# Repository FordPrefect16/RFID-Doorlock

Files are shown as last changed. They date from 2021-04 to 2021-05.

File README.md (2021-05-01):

# RFID-Doorlock
A 3D-printable Doorlock which can attached to a standard door lock cylinder. Opens via RFID-Tag

Aim of this project is to create a electronic doorlock for access control and logging on an sd card. It shall be used on the door of the makerspace at our University. 

The first version of this lock will rely on a wireconnection between outer and inner parts of the lock, hopefully later versions will communicate over radio. 
STL an CAD files can be found under main.

### Short description of planed functions

The mechanism at the inside of the door is shoved over the key and can be secured with two screws at the fittings and two additional screws. Also the cylinder is secured with a press fitting. When a RFID Tag is registered at the door terminal, the tag will be compared to the entitled codes on a csv-file on sd. When access is granted, the buttons (which indicate the lockstate via LED - open or closed) can be pressed. The green one opens the lock, the red one closes it. Tag, time, date and action will be logged on a csv-file. The lockstate is retrieved through a 10 turn potentiometer, to secure right Information, even if lockstate is changed to mechanical action. The lock can be manualy overridden from inside by turning the wheel or from outside with the right key for the cylinder. 
 


# Materials used

Printed in black PLA on a Ender 3

### List of materials (inside mechanics):



- 1x cylinder with key used in door
- 1x bearing 6808 2RS / 61808 2RS 40x52x7 mm
- 1x timing belt GT2 288 mm 
- 1x timing belt GT2 174 mm
- 1x Nema 17 stepper motor 42x20 mm, 16 Ncm, 1 A, biopolar
- 1x 10K Potentiometer 10 Turn
- 5x M3*20
- 4x M3*16
- 2x M2*20 + Nut
- 6x M4*10
- 4x M3*20 countersunk head

### List of materials (controller/electronics):



- Arduino UNO <br>
- 1x power supply 9-12 V (for this setup 9 V are recomended so the A4988 driver can supply the stepper with 1 A without overheating)
- 1x jack connector for breadboard
- 1x Protobreadboard halfsized
- Dupont-connectors
- 1x 100 uF electrolyte capacitor
- 1x stepper driver (e. g. A4988) (don't forget to adjust current output for Stepper)
- 1x Adafruit MicroSD Card Breakout Board (with SPI) + micro SD (for Access control + data logging)
- 1x RTC Breakout Board - Real Time Clock

For wireless version:
- radio component(NRF24L01)

### List of materials (door terminal):



- 4x M3*4
- 4x M4*6
- 1x pieco beeper (active) 5 V
- JST-connectors
- 1x 100 uF electrolyte capacitor
- 1x button / led red, 5 V, 10 mm
- 1x button / led green, 5 V, 10 mm
- 1x PN532 NFC RFID Module Elchouse (in this setup I2C is used, don! forget to setup the switches on this breakout board)
- 1x Protobreadboard halfsized
  
For wireless version: 
- Arduino Nano
- radio component(NRF24L01)
   
### Mechanism without hull



### Circuit




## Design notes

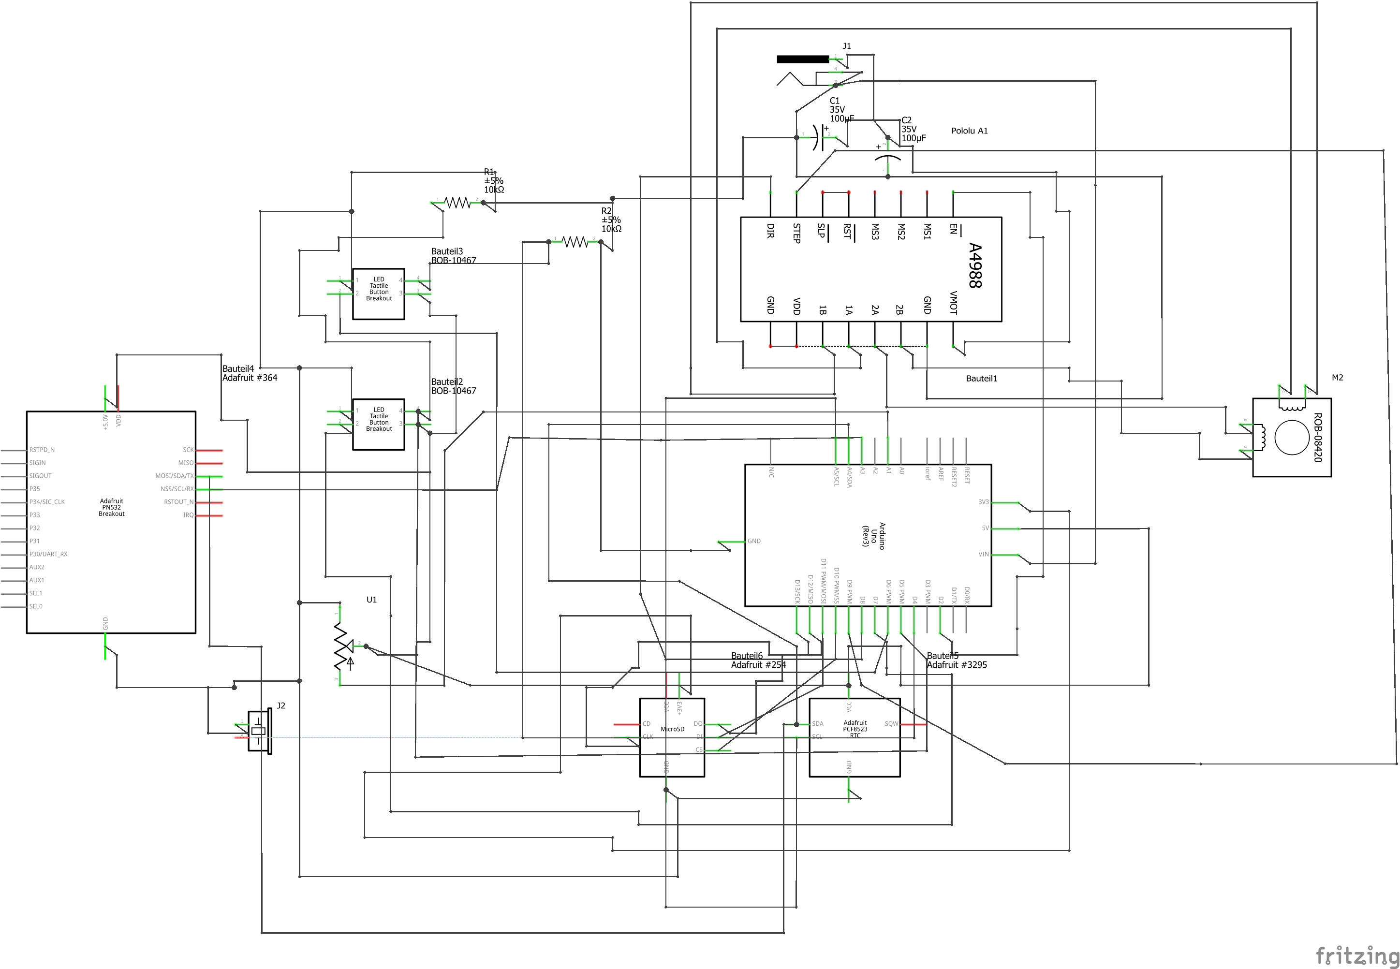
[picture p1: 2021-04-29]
Schematics/Circuit_fritzing_cable_Schaltplan.png

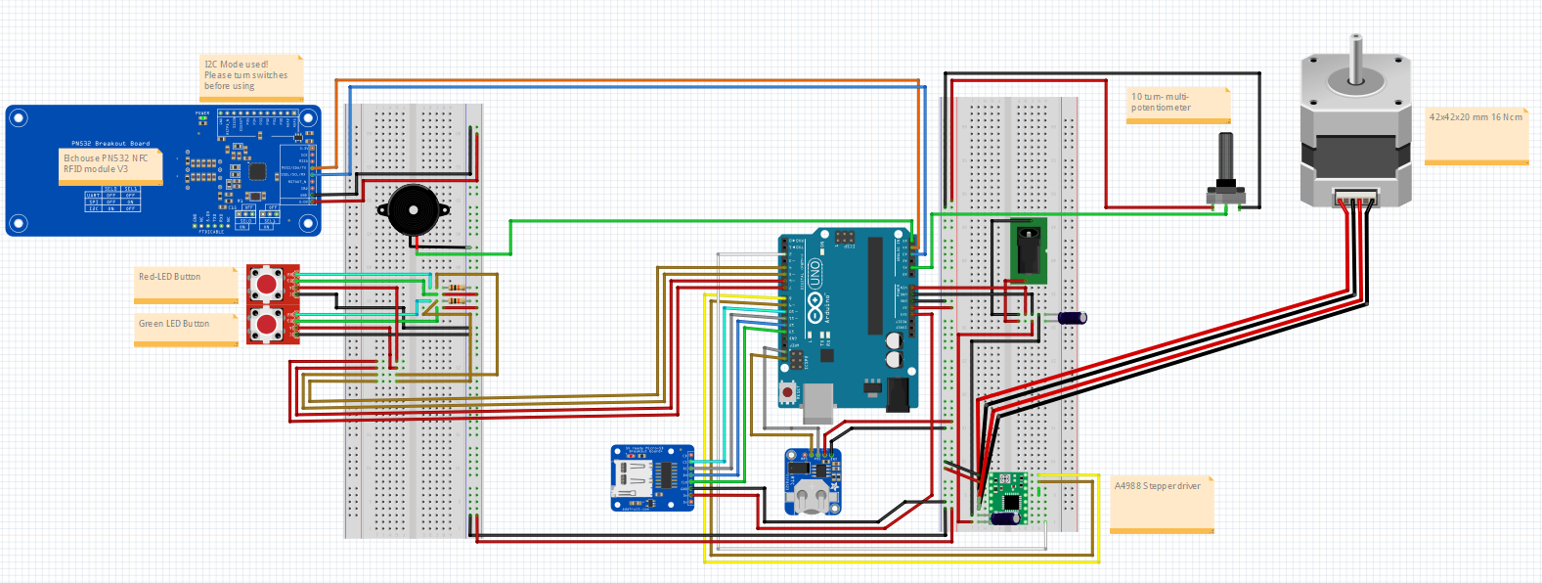
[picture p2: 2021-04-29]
Schematics/Schematics.PNG

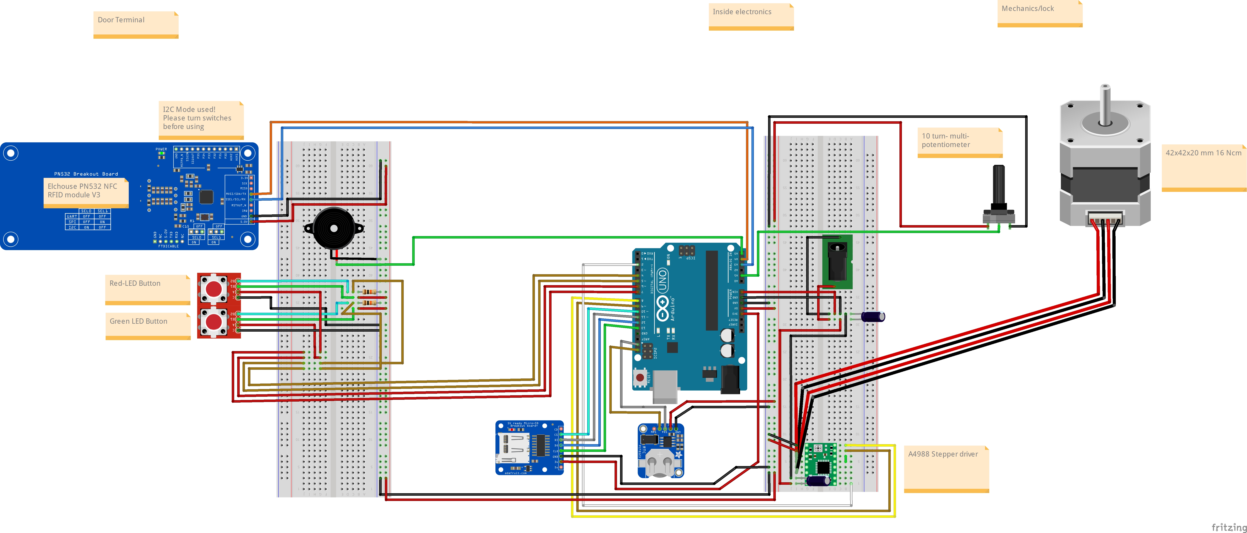
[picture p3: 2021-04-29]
Schematics/Circuit_fritzing_cable_Steckplatine.jpg

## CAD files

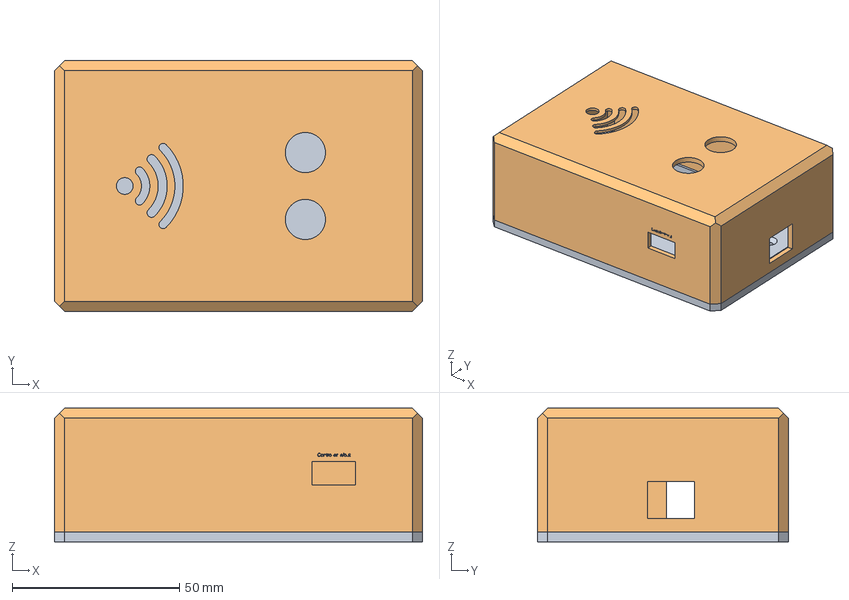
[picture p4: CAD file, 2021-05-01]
Printable Parts/CAD/DoorTerminal.step
110.0 x 75.0 x 40.0 mm

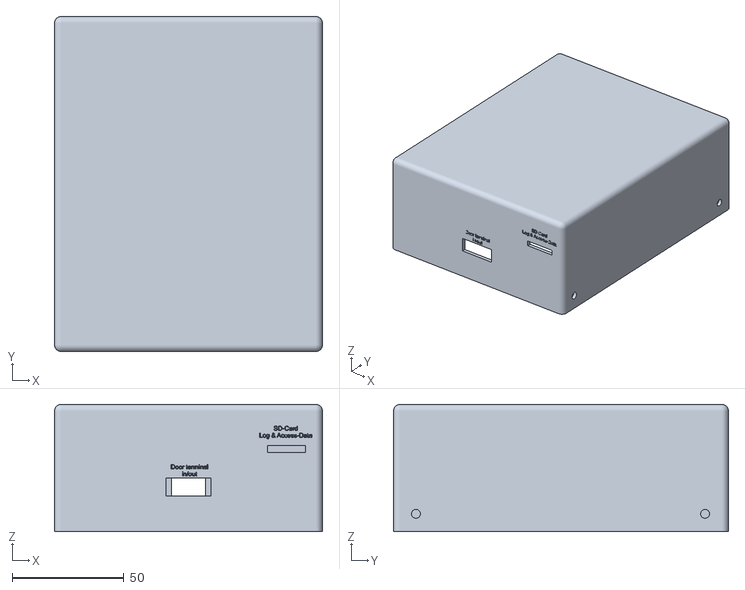
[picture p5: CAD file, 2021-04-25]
Printable Parts/ControlerElectronics/Electronics-Top.stl
120.0 x 150.0 x 57.0

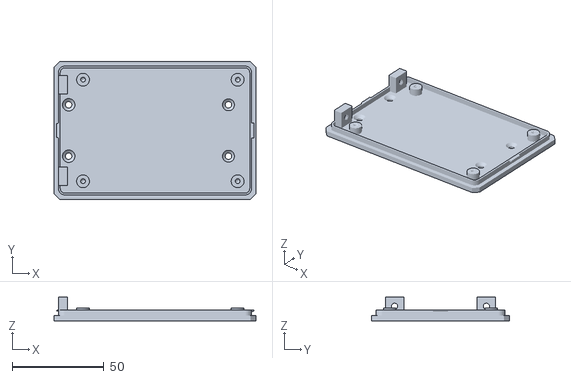
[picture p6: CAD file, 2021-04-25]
Printable Parts/Door Terminal/Door terminale base.stl
110.0 x 75.0 x 13.0

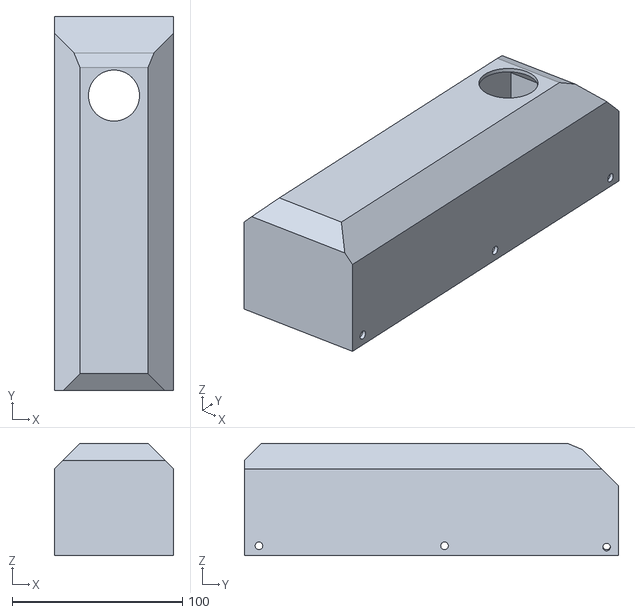
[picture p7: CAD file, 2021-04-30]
Printable Parts/Mechanics/Lock-Top-V2.stl
70.0 x 220.0 x 66.0

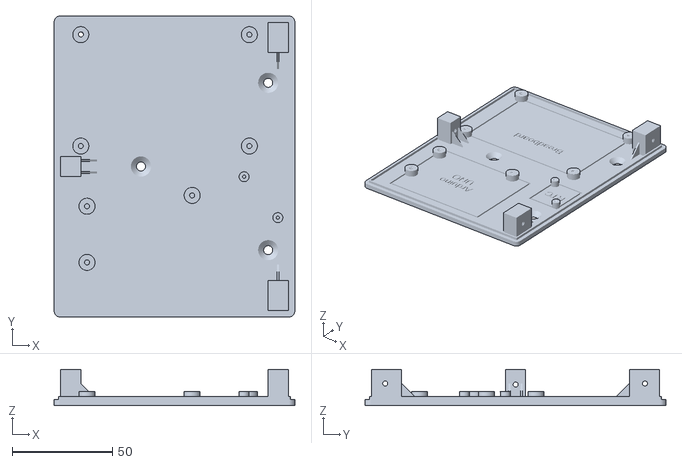
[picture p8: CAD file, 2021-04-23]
Printable Parts/ControlerElectronics/Electronics-Base.stl
120.0 x 150.0 x 18.0

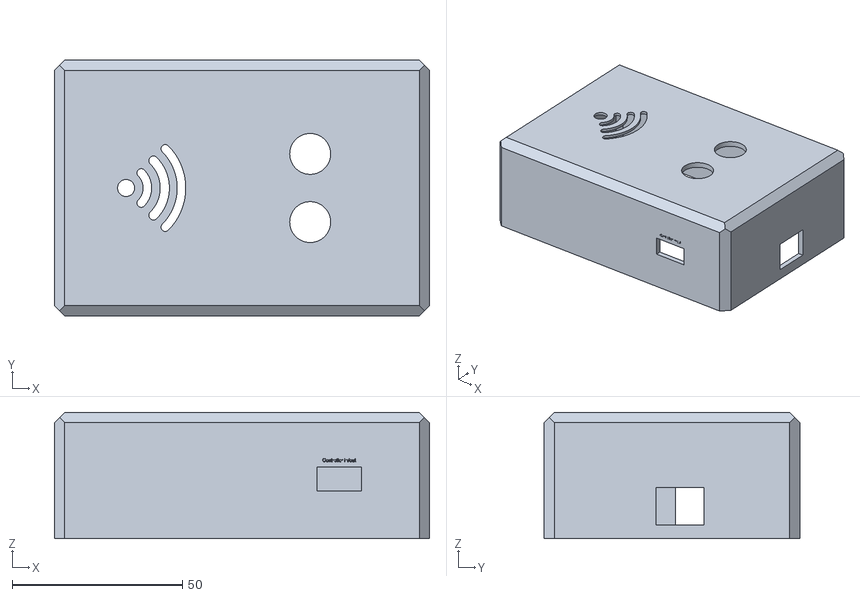
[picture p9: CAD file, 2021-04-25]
Printable Parts/Door Terminal/Door terminale top.stl
110.0 x 75.0 x 37.0

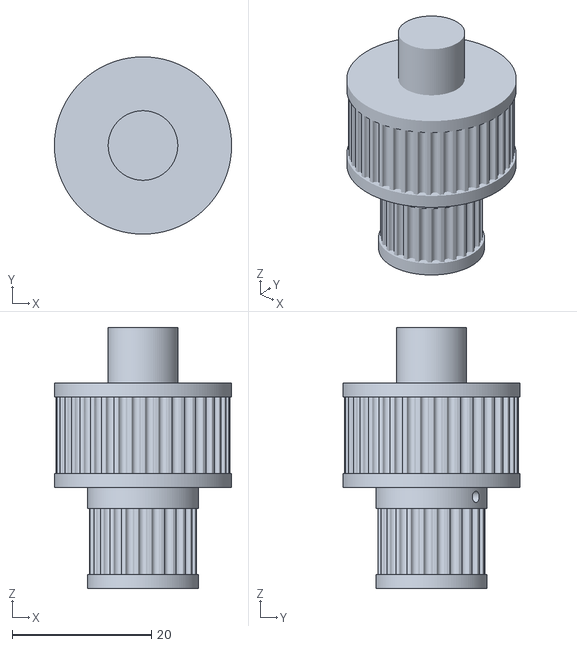
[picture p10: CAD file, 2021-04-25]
Printable Parts/Mechanics/Lock-Pulley.stl
25.5 x 25.5 x 37.5

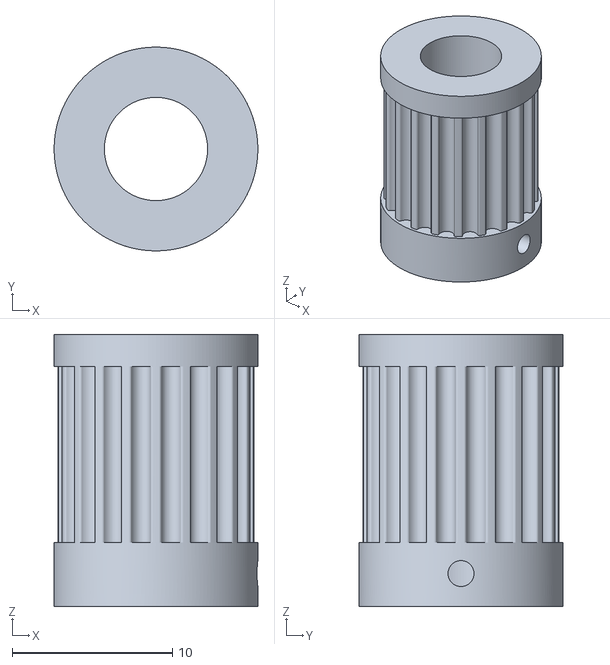
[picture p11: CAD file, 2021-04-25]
Printable Parts/Mechanics/Lock-Pulley2.stl
12.7 x 12.7 x 17.0

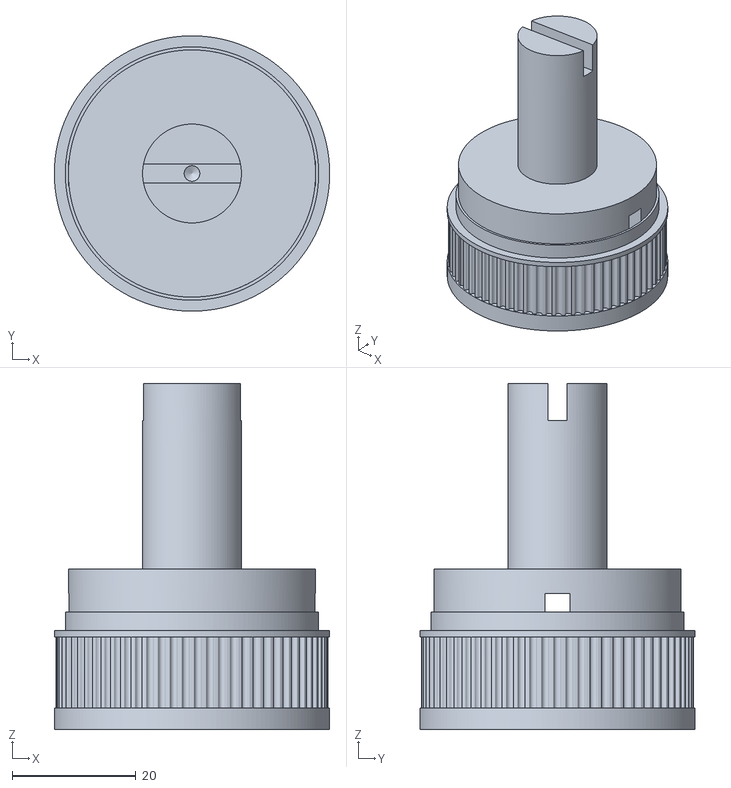
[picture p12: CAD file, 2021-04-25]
Printable Parts/Mechanics/Lock-Key-Holder.stl
44.6 x 44.6 x 56.0

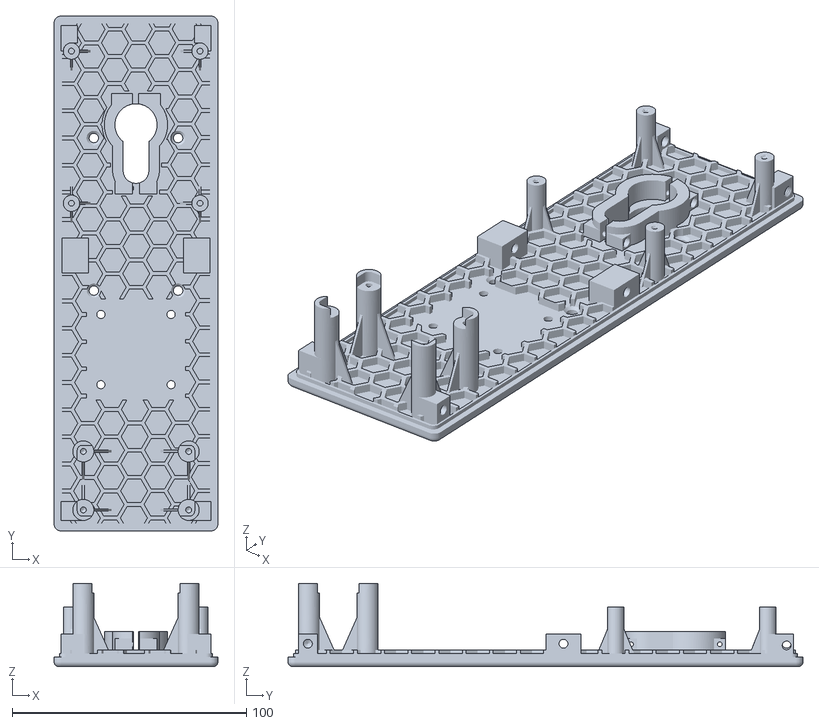
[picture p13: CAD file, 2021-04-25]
Printable Parts/Mechanics/Lock-Base.stl
70.0 x 220.0 x 35.5

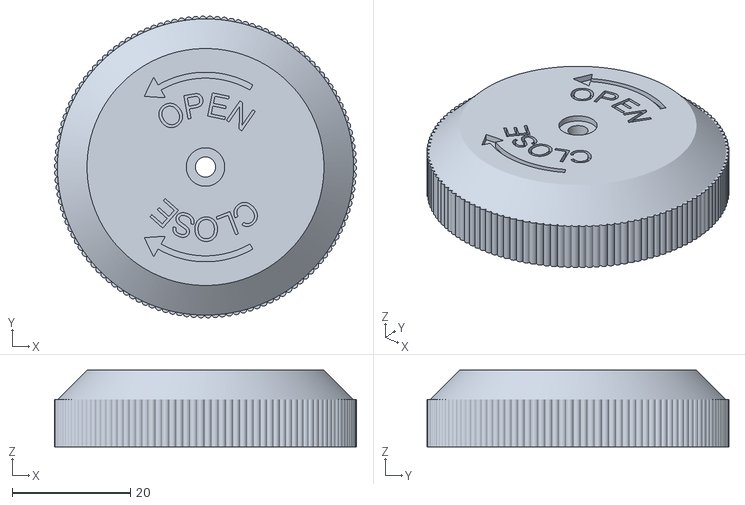
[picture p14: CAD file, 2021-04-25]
Printable Parts/Mechanics/Lock-Wheel.stl
51.0 x 51.0 x 13.0

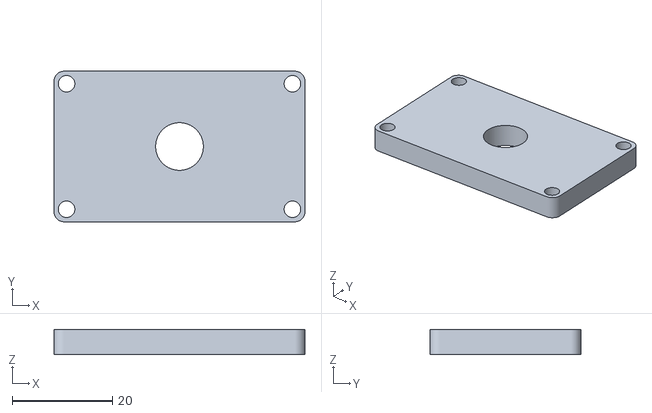
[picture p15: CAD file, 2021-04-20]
Printable Parts/Mechanics/Lock-Poti-Holder.stl
50.0 x 30.0 x 5.00

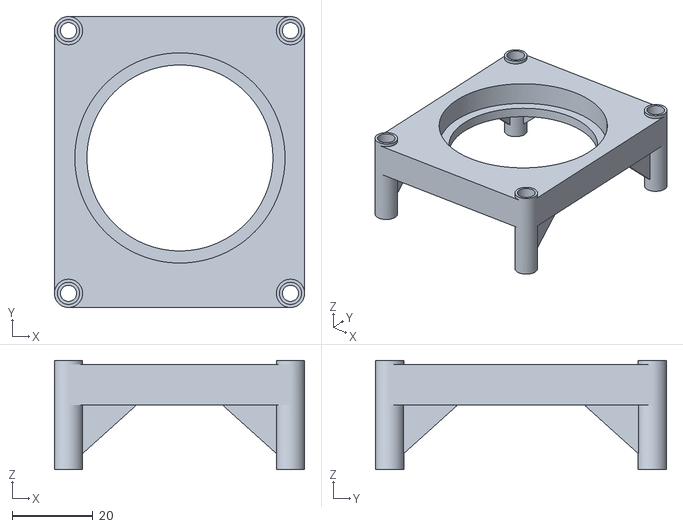
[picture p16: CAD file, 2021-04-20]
Printable Parts/Mechanics/Lock-Keyframe.stl
61.9 x 72.0 x 27.0

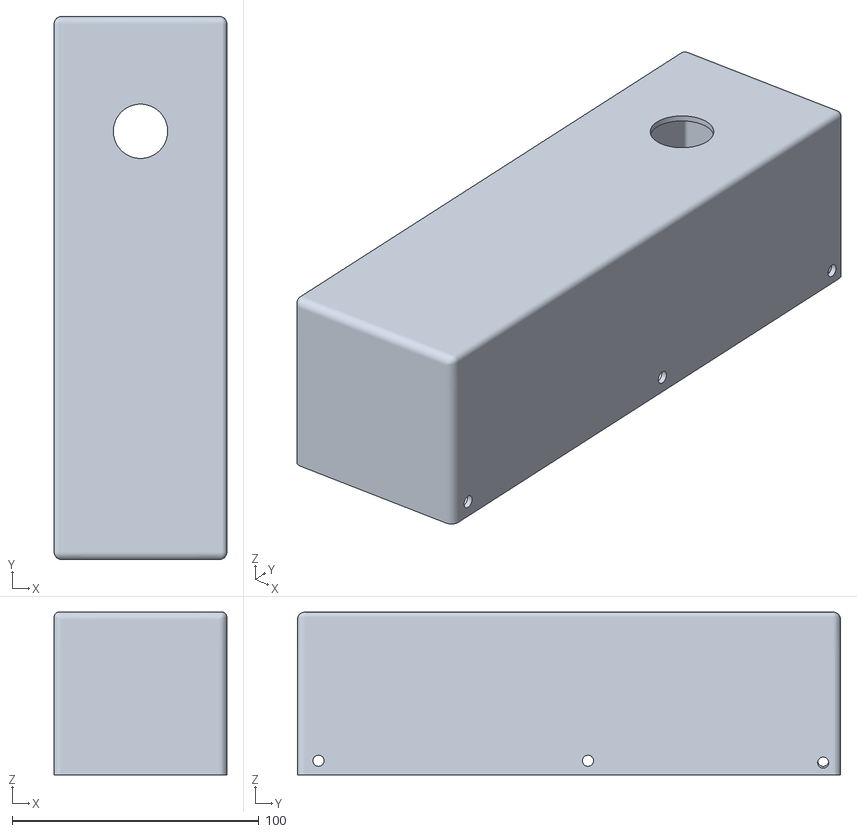
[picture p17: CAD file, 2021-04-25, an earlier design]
Printable Parts/Mechanics/Lock-Top.stl
70.0 x 220.0 x 66.0

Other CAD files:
Printable Parts/CAD/DoorTerminal.dxf
Printable Parts/Fusion360/DoorTerminal.f3d
Printable Parts/Fusion360/Electronics-Inside.f3d

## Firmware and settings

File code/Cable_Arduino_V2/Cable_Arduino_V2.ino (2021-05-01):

//Setup RTC

#include "RTClib.h"
RTC_PCF8523 rtc;

//Setup nfc

#include <NfcAdapter.h>
#include <PN532_I2C.h>
#include <PN532.h>
#include <Wire.h>
PN532_I2C pn532_i2c(Wire);
NfcAdapter nfc = NfcAdapter(pn532_i2c);

//Setup SD-Card

#include "SdFat.h"
#define SD_FAT_TYPE 0 //SD format = Fat32
const uint8_t SD_CS_PIN = 10;
#define SD_CONFIG SdSpiConfig(SD_CS_PIN, DEDICATED_SPI)
SdFat sd;
File file;
File myFile;
char line[21];

//Setup SPI
 
#include <SPI.h>
char UID2 [21];
String UID;

//Setup loop

long interval = 20000;       //change to wanted waiting time for pressing button
long prevTime = 1000;

//variables for lockstatus

int sensorValue = 0;

//pins

    //stepper
    const int stepPin = 9;   //steppercontrol-step
    const int dirPin = 8;    //steppercontrol-direction
    const int enablePin = 2;    //steppercontrol-enable
    int stepCounter;
    const int steps = 1500;     //maximum of steps, that should be done


    //buttons
    const int RedButtonPin = 4; 
    const int GreenButtonPin = 3; 
    const int RedLEDPin = 7; 
    const int GreenLEDPin = 6;

    //buzzer
    const int buzzPin = A3;

    //lockstatus input
    const int statusPin = A1;

    
void setup() {


pinMode(enablePin, OUTPUT);         //steppercontrol-enable 
pinMode(RedButtonPin, INPUT);       //red-button
pinMode(GreenButtonPin, INPUT);     //green-button
pinMode(GreenLEDPin, OUTPUT);       //green-led
pinMode(RedLEDPin, OUTPUT);         //red-led
pinMode(SD_CS_PIN, OUTPUT);         //SD-CS
pinMode(stepPin,OUTPUT);            //steppercontrol-step
pinMode(dirPin,OUTPUT);             //steppercontrol-direction
pinMode(statusPin, INPUT);          //lockstatus-potentiometer
pinMode(buzzPin, OUTPUT);           //buzzing
pinMode(A4, INPUT);                 //NFC-Reader-Input SDA
pinMode(A5, INPUT);                 //NFC-Reader-Input SCL
digitalWrite(stepPin, LOW);
digitalWrite(dirPin, LOW);
digitalWrite(enablePin, HIGH);      //disable Stepper

if (! rtc.begin()) {                                      //begin Real Time Clock script
    abort();
  }
             
//rtc.adjust(DateTime(F(__DATE__), F(__TIME__)));           //adjust time & date to computer time & date after initialisation or powerloss

if (rtc.lostPower()) {
    Serial.println("No Time set!");
    rtc.adjust(DateTime(F(__DATE__), F(__TIME__)));          //adjust time & date to computer time & date after initialisation or powerloss
    for(int x = 0; x < 900; x++) {
                  digitalWrite(buzzPin,HIGH); 
                  delay(100); 
                  digitalWrite(buzzPin,LOW); 
                  delay(500); 
                }
}

Serial.begin(9600);
Serial.println("NDEF Reader");
nfc.begin();


}

void loop() {
 

while (nfc.tagPresent()) {                                //scanning for NFC-Tag
  NfcTag tag = nfc.read();   
  Serial.println(tag.getUidString());
  UID = tag.getUidString();                               //buffering UserID as string 
  UID.toCharArray(UID2, 21);                              //string UserID to char for comparing to Access.csv    
  Serial.println ("comparing...");
  sd.begin(SD_CONFIG);                                    // Initialize SD-Card -> after changing SD-Card restart is mandatory!
  file.open("Access.csv");                                //open csv file with stored Tags
    while (file.available()) {
      Serial.println("reading line...");
      file.fgets(line, 21);                               //reading UserIDs from file
      if (strcmp(line, UID2)==0){
        file.close();                                     //closing file, & directory
        Serial.println("Access granted");
        digitalWrite(buzzPin, HIGH);                           //short beeping
        delay(10);
        digitalWrite(buzzPin, LOW);
        delay(5);
        prevTime = millis();                              //starting timer 
        while (millis() - prevTime <= interval){
          Serial.println("Waiting for button input...");
          if(digitalRead(GreenButtonPin) == HIGH) {                    //green button pressed
              Serial.println("Open lock..."); 
              delay(10);
              digitalWrite(enablePin,LOW);                //enable stepper
              digitalWrite(dirPin,LOW);                   //stepper moves in opening diriction
                for(stepCounter = 0; stepCounter < steps; stepCounter++) {
                  digitalWrite(stepPin,HIGH); 
                  delayMicroseconds(500); 
                  digitalWrite(stepPin,LOW); 
                  delayMicroseconds(500);
                  if(analogRead(statusPin)>1000){
                   break;
                  }
               }   
               if(analogRead(statusPin) > 840){         //turn on green LED/turn off red LED when lock open
                 digitalWrite(RedLEDPin, LOW);
                 digitalWrite(GreenLEDPin, HIGH);
               }
               if(analogRead(statusPin) <= 840){          //turn on red LED/turn off green LED when lock closed
                 digitalWrite(RedLEDPin, HIGH);
                 digitalWrite(GreenLEDPin, LOW);
               }
                
               delay(5000);
               digitalWrite(dirPin,HIGH);                //changes direction after 5 seconds to close latch
                 for(int x = 0; x < 100; x++) {
                  digitalWrite(stepPin,HIGH); 
                  delayMicroseconds(1000); 
                  digitalWrite(stepPin,LOW); 
                  delayMicroseconds(1000); 
                  
                  
                 }
               digitalWrite(enablePin, HIGH);               //disable stepper
               file.open("Log.csv", FILE_WRITE);         //opening Logging-File
               DateTime now = rtc.now();                 //reading date from RTC, optimize layout and print to Log.csv
               if(now.day()<10){
                file.print("0");
               }
               file.print(now.day(), DEC);
               file.print('-');
               if(now.month()<10){
                 file.print("0");
               }
               file.print(now.month(), DEC);
               file.print('-');
               file.print(now.year(), DEC);
               file.print(" ");
               if(now.hour()<10){
                 file.print("0");
               }
               file.print(now.hour(), DEC);              //reading time from RTC, optimize layout and print to Log.csv
               file.print(':');
               if(now.minute()<10){
                 file.print("0");
               }
               file.print(now.minute(), DEC);
               file.print(':');
               if(now.second()<10){
               file.print("0");
               }
               file.print(now.second(), DEC);
               file.print(" Lock opend by ");            //print action to file
               file.print(UID);                          //print UserID to file
               file.println();
               file.close();                             //close file
               delay(5);
               break;                                    //exit timer loop
         }
          if(digitalRead(RedButtonPin) == HIGH) {                   //red button pressed
             Serial.println("Closing lock...");
             digitalWrite(dirPin,HIGH);                  //changes the rotation direction zo closing
             digitalWrite(enablePin,LOW);                //enables stepper
              for(int x = 0; x < 900; x++) {
               digitalWrite(stepPin,HIGH); 
               delayMicroseconds(1000); 
               digitalWrite(stepPin,LOW); 
               delayMicroseconds(1000); 
               if(analogRead(statusPin)<290){
                 break;
               }
             }
          digitalWrite(enablePin, HIGH);                 //disable stepper
          file.open("Log.csv", FILE_WRITE);              //open Logging-File
          DateTime now = rtc.now();                      //reading date from RTC, optimize layout and print to Log.csv
          if(now.day()<10){
            file.print("0");
          }
          file.print(now.day(), DEC);
          file.print('-');
          if(now.month()<10){
            file.print("0");
          }
          file.print(now.month(), DEC);
          file.print('-');
          file.print(now.year(), DEC);
          file.print(" ");
          if(now.hour()<10){
            file.print("0");
          }
          file.print(now.hour(), DEC);                    //reading time from RTC, optimize layout and print to Log.csv
          file.print(':');
          if(now.minute()<10){
            file.print("0");
          }
          file.print(now.minute(), DEC);
          file.print(':');
          if(now.second()<10){
            file.print("0");
          }
          file.print(now.second(), DEC);
          file.print(" Lock closed by ");                //print action to file
          file.print(UID);                               //print UserID to file
          file.println();                      
          file.close();                                  //close file 
          delay(5);   
          break;                                         //exit timmer loop
          } 
        }
     }
      else{
        Serial.println("FALSE");
      }
      
    }
  }
  

sensorValue = analogRead(statusPin);                           //watching lockstate
Serial.print("Lockstatus: ");
Serial.println(sensorValue);
delay(10);
if(analogRead(statusPin) > 840){                                 //turn on green LED/turn off red LED when lock open
   digitalWrite(RedLEDPin, LOW);
   digitalWrite(GreenLEDPin, HIGH);
}
if(analogRead(statusPin) <= 840){                                 //turn on red LED/turn off green LED when lock closed
   digitalWrite(RedLEDPin, HIGH);
   digitalWrite(GreenLEDPin, LOW);
}

}

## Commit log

2021-04-20 Add files via upload
    3D-printable parts
    [Lock-Base.stl, Lock-Hull.stl, Lock-Key-Holder.stl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]
2021-04-20 Add files via upload
    Fusion360 CAD Files
2021-04-23 New Sorting
    Printable parts are now sorted by belionging unit: "Door Terminal", "Controller/Electronics", "Mechenics"
    [Lock-Base.stl, Lock-Hull.stl, Lock-Key-Holder.stl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]
2021-04-23 minor Update
    New printable parts added, list of materials in Readme.md adjusted
    [Door terminale base.stl, Door terminale top.stl, Electronics-Base.stl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]
2021-04-25 Update
    - Updated STL and CAD-Files to first working version
    - Added code
    [Door terminale base.stl, Door terminale top.stl, DoorTerminal.f3d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]
2021-04-28 Minor Update
    implemented failsafe for situation when lock is manually overridden and position is not properly restored
    [Cable_Arduino_V2.ino]
2021-04-29 Update
    Added Circuit Schematics
2021-04-29 Update
    Added Circutry
    [Circuit_fritzing_cable.fzz]
2021-04-30 Minor Update
    Added new model for Top
    [Lock-Top-V2.stl, Lock-Top.stl]
2021-04-30 Minor Update
    RTC notification when power lost
2021-05-01 Minor Fixes
    [DoorTerminal.dxf, DoorTerminal.step]
